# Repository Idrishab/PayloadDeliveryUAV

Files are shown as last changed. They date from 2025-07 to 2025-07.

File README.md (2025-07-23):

# Payload_Delivery_UAV
This project was developed as part of the Aircraft Design course during my undergraduate studies at Kwara State University in 2017. It began as a personal endeavor and later evolved into a course project. The design process focused on manufacturability, with constraints shaped by personal funding and access to local workshops.

The UAV was designed with a maximum takeoff mass (MTOM) constraint of 1.2 kg. Design calculations and optimization were carried out using MATLAB scripts, while CAD modeling was performed in SolidWorks. Aerodynamic properties of various airfoils were analyzed using XFOIL to inform the final design choices.

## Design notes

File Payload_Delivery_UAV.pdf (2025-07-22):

# DESIGN OF A 1.2Kg PAYLOAD DELIVERY UAV

BY

## IDRIS HABEEB BABATUNDE

AS

## ASSESSMENT FOR AIRCRAFT DESIGN

## AAE 401

## DEPARTMENT OF AERONAUTICAL AND ASTRONAUTICAL ENGINEERING

## KWARA STATE UNIVERSITY

## INSTRUCTOR

# DR. YOMI OBIDI

### SUBMISSION DATE: JUNE 15, 2017

## Table of Contents

## ABSTRACT

The design approach used (in this work) is basically the system engineering approach. The detailed description of the design processes and stages involved in this work were presented based on the steps followed.

First pass design was done based on the information acquired from the mission profile, customer design specifications and design objectives. The customer design specifications were incorporated into the conceptual design which provided guidelines through the whole design processes where various adequate equations were applied to obtain the desired parameters. Reasonable guesses were made and various tables were consulted in some instances where there were no available befitting mathematical equations to get the actual required values.

In some instances, the weight of the aircraft is assumed to be constant because it will be using a battery and the payload weight (after dropping it) has no significant change in the weight. Center of gravity (CG) position is also assumed to be constant because the store (for the payload) is situated directly under the CG position which led apparently, to no change in the CG position after releasing the payload.

During the design processes, some parameters of already designed components were reviewed to satisfy the requirements of other components. Federal Aviation Regulations (FAR) were followed and some rules of thumb were applied. Lots of materials resources were also considered to complete this work as all the required information can’t be obtained from a single materials.

# CHAPTER 1

INTRODUCTION
This design is a RC (remote controlled) UAV whose range depends on both battery and transmitter frequency (to maintain transmitter-receiver communication for control) and the endurance depends solely on the battery. The design order is based on the extent of the required parameters which is the reason why the wing was designed immediately after the initial sizing and the tail plane was designed after the wing. The control surfaces were deemed to be designed after all other aircraft components have been designed because of the complexity of the required information.

Aircraft design is an iterative process which requires various parameters to be altered, over and over again, to satisfy various requirements. To make the iteration easy, accurate and to save time, the equations are transformed into MATLAB codes. In calculating the actual lift generated by lifting surfaces, lifting line theory was employed and all the steps involved in it were embedded in a MATLAB program.

Generally, in design, computer aided design (CAD) software are used. The CAD software used for this design is Solidworks. After designing each component, 3D designs of each of the components was produced and were assembled at the end of the whole design process.

# CHAPTER 2

MISSION PROFILE
The aircraft will takeoff within a ground roll of about 8m, climb to an altitude of 15m, within 30 seconds, cruise for some time to cover a distance around 100m, then, loiter around for about 10 seconds to drop a light payload (of about 10g of mass). The aircraft will then return and land with a maximum ground roll of 12m. The flight time will be around 5 minutes and the takeoff mass shouldn’t be more than 1.2kg. The stall speed should not exceed 8m/s and maximum speed should not be less than 15m/s.

From above, the following were deduced:

1. STO = 8m
2. Slanding = 12m
3. Cruise altitude = 15m
4. Vstall = 8m/s
5. Vmax = 15m/s
6. ROC = 15m/30s = 0.5m/s
7. Endurance = 10s
8. Range = about 150m
9. Flight time = 5min
10. MTO = 1.2kg

DESIGN OBJECTIVES
Listed below, are the design objectives commonly considered in designing an aircraft. They were used as guidelines during the design process. Because it is impossible to satisfy all these objectives at once, they were arranged based on their importance to this design.
1. Low cost
2. Control and stability
3. Light weight
4. Ease of manufacture
5. Aerodynamic performance
6. Structural Integrity
7. Heavy payload

# CHAPTER 3

CONCEPTUAL DESIGN
Proposed aircraft: 1.2kg, single engine, prop-driven light-weight UAV

Intended use: object dropping (alternative use is surveillance)

Numbers of seats: no seat

Range: about 150m

Rate of climb: 0.5m/s

Fuel capacity: NIL

Engine selection: Brushless electric motor.

Velocities
1. Max speed: 15m/s
2. Cruise speed: 11.538m/s (i.e. Vmax/1.3)
3. Stall speed: 8m/s
4. Landing speed: 10.4m/s (i.e. 1.3Vstall)

Takeoff and Landing Requirement
1. Takeoff ground roll: 8m
2. Landing ground roll: 12m

Wing Configuration
1. Number of wings: monoplane
2. Wing location: High wing
3. Wing type: Rectangular (because of weight, cost and ease of manufacture)
4. High lift device: Plain flap
5. Shape: Fixed shape
6. Structural configuration: Cantilever

Tail Configuration
1. Tail location: Aft tail
2. Horizontal and vertical tails: conventional tail
3. Attachment: Fixed

Landing Gear Configuration
1. Landing gear mechanism: Fixed

2. Landing gear type: Tricycle
3. Runway: Land based

Manufacturing-Related Item Configuration
1. Material for manufacturing: Foam (Styrofoam, foam board or any other)
2. Assembly technique: use of glue, screws and bolts & nuts

Subsystems Configuration
1. Primary control surfaces: conventional (i.e., elevator, aileron and rudder)
2. Secondary control surface: High lift device (flap)
3. Power transmission: fly-by-wire
4. Fuel tank: inside fuselage (battery)
5. Storage: light object (payload of about 10g)

# CHAPTER 4

FIRST PASS DESIGN
1. Payload mass: 10g
2. Gross weight: 11.772N (i.e. 1.2Kg)
3. Wing loading

Wg
Se

=

ρoVstall

2

2

CLmax
(4.1)
Where ρo = 1.225kg/m³
, Vstall = 8m/s and CLmax was selected to be 1.6

Wg
Se

=

1.225×8

2

2

1.6 = 62.72N/m²
(4.2)

Vlanding = 1.3Vstall = 1.3 × 8 = 10.4m/s
4. Effective wing area,

Se =

Wg
(

Wg
Se

)

=

11.772
62.72

= 0.1878m²
(4.3)
5. Dynamic pressure

q =

ρσVcr

2

2

(4.4)
Where air density and relative density (at cruising altitude (15m)), are 1.2232kg/m³ and 0.9986 respectively. Cruising speed is 11.538m/s

q =

1.2232 ∗ 0.9986 ∗ 11.538²
2

= 81.31N/m²

6. Coefficient of lift at cruise

CL =

Wg⁄Se
q

=

62.72
81.31
= 0.7714 | (4.5)

CL =

1
F

∴ F =

1
CL

=

1
0.7714
= 1.2964 | (4.6)
7. Coefficient of drag

CD = CDP +

CL

2 πeAR | (4.7)

Where CL = 0.7714, CDP was selected to be 0.025, e to be 0.825 and AR to be 7

CD = 0.025 +

0.7714
π × 0.825 × 7

= 0.0578
8. L
D

=

CL
CD

=

0.7714
0.0578
= 13.346 | (4.8)
9. D = Wg ∙

CD
CL

= 11.772 ×

1
13.346
= 0.8821N | (4.9)
10. Thrust horsepower required at cruise altitude THP =

DVcr
745.7

=

0.8821∗11.538
745.7
= 0.01365ℎp (10.177W) | (4.10)
11. Maximum brake horsepower (BHP)

BHPcr =

THP

ηprop

⁄0.7 | (4.11)

ηprop was selected to be 0.85 BHPcr =

0.01365
0.85
⁄0.7 = 0.0229ℎp (17.1W) | (4.12)

BHP at sea level = BHPcr (

ρo
ρ

)

0.96
= 0.0229 (

1.225
1.2232)

0.96
= 0.023ℎp (4.13)
12. Optimum cruise lift coefficient
CL = √π ∙ e ∙ AR ∙ CDP = √π ∙ 0.825 ∙ 7 ∙ 0.025 | (4.14)

= 0.6735
Optimum Vcr = √
Wg
ρ
2

σ∙CLcropt

∙Se∙F

= √
11.772
1.2232
2

×0.6735×0.1878×1.2964

= 10.834m/s (4.15)

13. Power required to satisfy the required ROC:
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
3CDo
K

(

W
S

)∙(
1.155
(L⁄D)ηp

)

| (4.16)

Where W/P is the power loading, ROC is the rate of climb, ηp is the propeller efficiency, ρ is the air density at sea level, CDo is the zero lift drag coefficient, K is the induced drag factor, (W/S) is the wing loading, and (L/D) is the lift to drag ratio.
K =
1 π∙e∙AR | (4.17)

K =

1
3.142 × 0.825 × 7

= 0.0551

ROC has been stated earlier to 0.5m/s and CDo was selected to be 0.035.
(

W
P

) =

1

0.5
0.85 +

√
2
1.225 × √
3 × 0.035
0.0551

× 62.72 × (

1.155
13.346 × 0.85)

= 0.6636N/W

P =

W
(

W
P

)

(4.18)

P =

11.772
0.6636 = 17.7W

Therefore, the power required is 17.7W

FIRST PASS FINAL RESULT

1. Gross weight, Wg = 11.772N
2. Wing loading = 62.7N/m²
3. Stall velocity = 8m/s
4. Wing area = 0.1878m²

5. Dynamic pressure, q = 81.3N/m²
6. Total drag coefficient, CD = 0.0578
7. Lift to drag ratio = 13.346
8. Drag, D = 0.8821N
9. Thrust horsepower (THP) = 0.0136hp (10.177W)
10. Brake horsepower at cruise altitude (BHP)cr = 0.0229 (17.1W)
11. BHP at sea level = 0.023hp
12. Optimum cruise lift coefficient = 0.6735
13. Optimum cruise speed = 10.834m/s
14. ROC = 0.5m/s

SECOND PASS DESIGN
Second pass design wasn’t considered (because it involves obtaining a more accurate gross weight); the gross weight used during first pass design was stated as a requirement. Fuel and oil weights aren’t needed because the aircraft will be using a RC electric motor and battery. Second pass design also optimizes the wing area, drag and brake horsepower at sea level by multiplying them by a conversion factor (calculated using a new gross weight). Since the gross weight won’t be altered, these and other parameters obtained from first pass design will remain the same.

# CHAPTER 5

WING AIRFOIL SELECTION
PRACTICAL STEPS IN SELECTING AN AIRFOIL
1. Aircraft weight: 11.772N
2. Aircraft ideal cruise lift coefficient (CLC): CLC =

2Wavg
ρVC

2S

(5.1)

CLC =

2 × 11.772
1.2232 × 10.834² × 0.1878 = 0.8732
3. Wing cruise lift coefficient (CLCW ).

CLCW

=

CLC
0.95

(5.2)

CLCW

=

0.8732
0.95 = 0.9191
4. Wing airfoil ideal lift coefficient (Cli):

Cli =

CLCW

0.9

(5.3)

Cli =

0.9191
0.95 = 1.0212
5. Aircraft maximum lift coefficient (CLmax):

CLmax =

2WTO
ρ0Vs

2S

(5.4)

Where Vs is the aircraft stall speed, ρo is the air density at sea level, and WTO is the aircraft maximum take-off weight.

CLmax =

2 × 11.772
1.225 × 8

2 × 0.1878 = 1.6

6. Wing maximum lift coefficient (CLmax _w ).

CLmax _w =

CLmax
0.95

(5.5)

CLmax _w =

1.6
0.95 = 1.6832
7. Airfoil gross maximum lift coefficient (Clmax_gross):

Clmax _gross =

CLmax _w
0.9

(5.6)

Clmax _gross =

1.6832
0.9

= 1.8703

8. High lift device (HLD): Plain Flap.
9. HLD contribution to the wing maximum lift coefficient (ΔClHLD): 0.55.

10. Wing airfoil net maximum lift coefficient (Clmax):
Clmax = Clmax _gross − ∆ClHLD = 1.3203 | (5.7)
11. Reynolds number: 100,000 (using cruise speed and chord length of 10.834m/s and 0.16m respectively)

The following airfoils were considered

1. SD7037
2. E193
3. S9000
4. Clark Y

At Reynolds number of 100000, the values for various parameters (as shown in the table below) were obtained for the airfoils. These values were obtained with the aid of system software (XFOIL) and a website (www.airfoiltools.com)

AIRFOIL
PARAMETERS

AIRFOILS
| SD7037 | E193 | S9000 | CLARK Y
Clmax | 1.3364 | 1.283 | 1.2702 | 1.3663
Alfas (deg) | 12 | 12 | 11 | 12
Alfa0 (deg) | -1.7679 | -3.2868 | -1.2702 | -2.2492
Cl0 | 0.3046 | 0.4068 | 0.2071 | 0.3713
Cdmin | 0.01519 | 0.01452 | 0.01311 | 0.01722
Cli | 0.04 | 0.24 | 0.08 | 0.8
(Cl/Cd)max | 55.2 | 58.7 | 53.3 | 53
Clalfa | 6.0628 | 6.1183 | 6.0628 | 6.1852
Cmmin | -0.084 | -0.096 | -0.073 | -0.092
S.Q. | Moderate | Abrupt | Moderate | Docile
Max. thickness (unit) | 0.092 | 0.102 | 0.09 | 0.1171

From these, Clark Y airfoil was selected.

Table 5.1: Airfoil data

WING DESIGN
STEP 1: Wing incidence

The selected airfoil ideal lift coefficient is 0.8. Since at ideal lift coefficient, minimum drag is experienced, the angle of attack corresponding to the ideal lift coefficient was set as the wing incidence (or wing setting angle). To obtain this value, a reference was made to the Cl-α curve (through the use of XFOIL).

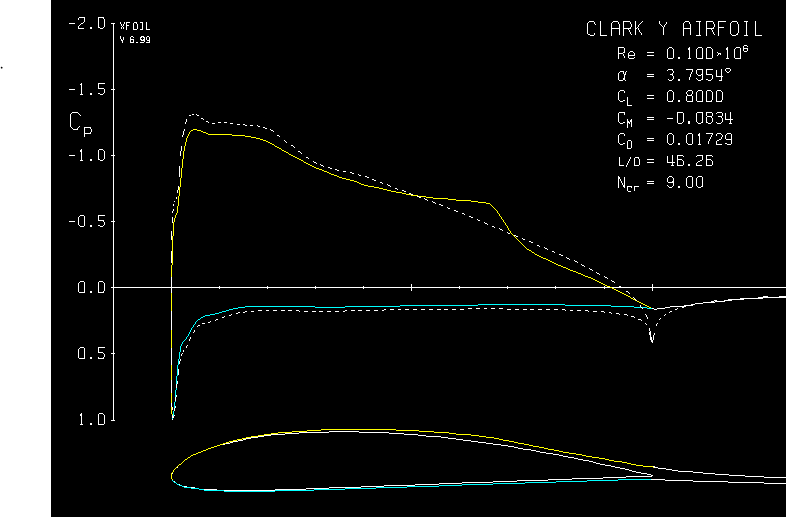
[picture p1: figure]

Therefore, wing setting angle (αset) or wing incidence (iw) is equal to 3.7954 deg.

STEP 2: ASPECT RATIO

Considering the various advantages and disadvantages of high and low values, aspect ratio was selected to be 7.

STEP 3: TAPER RATIO

The effects of taper ratio was carefully considered but for some reasons (such as ease of manufacturing, cost and to keep the design simple) the wing was left straight i.e. no taper.

Fig 5.1: wing setting angle from XFOIL

STEP 4: SWEEP ANGLE:

It was stated (in ref 1) that If the aircraft maximum speed is less than Mach 0.3 (the borderline to include the compressibility effect), no sweep angle is recommended for the wing, since its disadvantages will negate all the improvement produced. For this reason and some others, no sweep angle was considered.

STEP 5: TWIST ANGLE

This design will use no twist angle. Though, twist angle have the advantages of avoiding tip stall before root stall and modification of the lift distribution to an elliptical one but it give rise to reduction in lift. In addition, the complexity of manufacturing, increase in weight as well cost required prevent its use.

STEP 6: DIHEDRAL ANGLE

No dihedral.

STEP 7: REQUIRED LIFT COEFFICIENT DURING CRUISE:

CLC =

2Wavg
ρVc

2S

(5.8)

CLC =

2 × 11.7720
1.2232 × 10.834² × 0.1878 = 0.8732
STEP 8: REQUIRED AIRCRAFT TAKEOFF LIFT COEFFICIENT:
VTO = kVstall | (5.9)

Where k is 1.1 for fighter aircraft and 1.2 for general aviation (GA) aircraft

VTO = 1.2 × 8 = 9.6m/s

CLTO =

2WTO
ρVTO

2 S

(5.10)

CLTO =

2 × 11.7720
1.225 × 9.6

2 × 0.1878 = 1.1105

STEP 9: WING INCIDENCE FROM LIFTING LINE THEORY TO SATISFY CRUISE CL

A MATLAB code has been written (in Ref 1) for lifting line theory which divides the wing into sections to calculate the lifts generated per section. They were then summed up to obtain the total lift produced by the wing at that incidence. This MATLAB program has lift distribution curve incorporated in it.

The following were used in calculating lift coefficient at cruise

1. Wing area = 0.1878m²
2. Aspect ratio = 7
3. Taper ratio = 1
4. Twist angle = 0
5. Wing setting angle = 3.7954deg
6. Airfoil lift curve slope = 6.1852rad⁻¹
7. Zero-lift angle of attack = -2.2492deg

MATLAB CODE

clc
clear
N = 9; % (number of segments - 1) S = 0.1878; % m^2
AR = 7; % Aspect ratio
lambda = 1; % Taper ratio
alpha_twist = -1e-8; % Twist angle (deg)
i_w = 3.7954; % wing setting angle (deg)
a_2d = 6.1852; % Airfoil lift curve slope (1/rad) alpha_0 = -2.2492; % zero-lift angle of attack (deg)
b = sqrt(AR*S) % wing span (m)
MAC = S/b % Mean Aerodynamic Chord (m)
Croot = (1.5*(1+lambda)*MAC)/(1+lambda+lambda^2); % root chord (m) theta = pi/(2*N):pi/(2*N):pi/2;
alpha = i_w+alpha_twist:-alpha_twist/(N-1):i_w;
% segment’s angle of attack
z = (b/2)*cos(theta);
c = Croot * (1 - (1-lambda)*cos(theta)); % Mean Aerodynamics Chord at each segment (m)
mu = c * a_2d / (4 * b);
LHS = mu .* (alpha-alpha_0)/57.3; % Left Hand Side
% Solving N equations to find coefficients A(i):
for i=1:N
for j=1:N
B(i,j) = sin((2*j-1) * theta(i)) * (1 + (mu(i) * (2*j-1)) /sin(theta(i))); end
end
A=B\transpose(LHS);
for i = 1:N
sum1(i) = 0;
sum2(i) = 0;
for j=1:N
sum1(i) = sum1(i) + (2*j-1) * A(j)*sin((2*j-1)*theta(i)); sum2(i) = sum2(i) + A(j)*sin((2*j-1)*theta(i));
end
end
CL = 4*b*sum2 ./ c;
CL1=[0 CL(1) CL(2) CL(3) CL(4) CL(5) CL(6) CL(7) CL(8) CL(9)]; y_s=[b/2 z(1) z(2) z(3) z(4) z(5) z(6) z(7) z(8) z(9)]; plot(y_s,CL1,'-o')
grid title('Lift distribution') xlabel('Semi-span location (m)') ylabel ('Lift coefficient') CL_wing = pi * AR * A(1)

With these, the lift coefficient produced by the wing is 0.4898. The wing incidence was then varied via trial and error to obtain the required lift coefficient at cruise. At a wing incidence of 8.53deg, the generated wing lift coefficient is 0.8735. Although, this satisfies cruise requirement (based of lift coefficient) but the incidence is too high and the design has to be reviewed.

The major aim of reviewing the design is to reduce the required cruise lift coefficient which can easily be done by increasing the cruise speed. Cruise speed is a function of maximum speed (Vcr = Vmax/1.3). Therefore, maximum speed was adjusted to 19m/s. first pass design was then reviewed and the following are the new data:

1. Gross weight, Wg = 11.772N
2. Wing loading = 62.7N/m²
3. Stall velocity = 8m/s
4. Cruise speed = 14.6154m/s
5. Maximum speed = 19m/s
6. Landing speed = 10.4m/s
7. Wing area = 0.1878m²
8. Dynamic pressure, q = 130.4605N/m²
9. Cruise lift coefficient = 0.4808
10. Total drag coefficient, CD = 0.0377
11. Lift to drag ratio = 12.7394
12. Drag, D = 0.9241N
13. Thrust horsepower (THP) = 0.0181hp (13.497W)
14. Brake horsepower at cruise altitude (BHP)cr = 0.0304 (22.67W)
15. BHP at sea level = 0.0305hp (22.74W)
16. ROC = 0.5m/s

While reviewing airfoil selection criteria, the new required airfoil ideal lift coefficient is 0.5612. Reynolds number also changes to 150,000. At this Reynolds number, Clark Y airfoil has the following parameters:

1. Zero-lift angle of attack = -3.1264deg
2. Lift at zero AOA = 0.4345
3. Maximum Cl = 1.3769

4. Stall AOA = 13deg
5. Cdmin = 0.01244
6. Cli = 0.49
7. (L/D)max = 64.68
8. Cmmin = -0.099
9. Clα = 6.1852rad⁻¹

While reviewing wing design the following steps has these new results:

Step1: wing incidence equals 0.5327deg

Step 7: required lift coefficient during cruise is 0.48

With the use of the same MATLAB program, at a wing incidence of 2.8deg, the lift generated is 0.4808 and the lift distribution is as in the figure below. Therefore, the wing incidence was set to be 2.8deg.

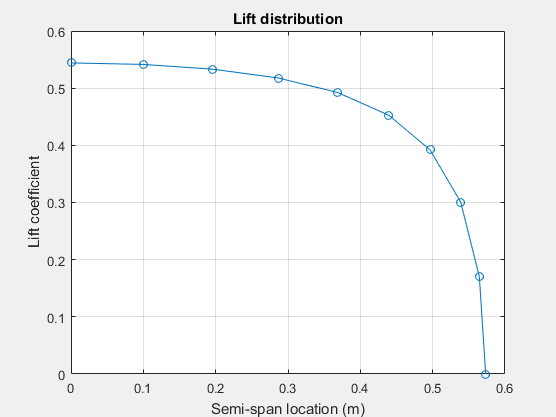
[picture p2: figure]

Although, the lift distribution is not elliptical but can be worked with as it is close to elliptical lift distribution. To achieve an elliptical lift distribution, the twist angle will have to be altered (to

Fig 5.2: Lift distribution around -1.5deg). Considering ease of manufacturing, light weight and cost; the twist angle was left unaltered.

STEP 10: FLAP DESIGN

In designing the flap, flap; span to wing span ratio (bf/b); chord to wing chord ratio (Cf/C) and; maximum deflection (δfmax) were used. The latter two were used to determine the approximate increment in the wing zero-lift angle of attack (due to flap deflection) through the use of the following equation:

∆∝o≈ −1.5 ∙

Cf
C
δf | (5.11)

Flap span to wing span ratio was used to determine the flap region across the span. These were incorporated into the MATLAB code for lifting line theory to determine the total lift generated by the wing (with flap down).

As an initial value, the following were used: Cf/C = 20%, bf/b = 60% and δf = 13deg and αTO = 9deg (wing angle of attack at takeoff)

With these, the total lift generated is 1.1863. When the wing angle of attack was set to 8.07deg, the lift generated by the wing is 1.1109. The wing angle of attack was reduced because of stall; the wing stalls earlier when flap is deflected.

MATLAB CODE WITH FLAP DEFLECTED

clc
clear
N = 9; % (number of segments-1) S = 0.1878; % m^2
AR = 7; % Aspect ratio
lambda = 1; % Taper ratio
alpha_twist = -1e-10; % Twist angle (deg)
i_w = 8.07; % wing setting angle (deg)
a_2d = 6.1852; % lift curve slope (1/rad)
a_0 = -3.1264; % flap up zero-lift angle of attack (deg)
cf_c=0.2; %flap to wing chord ratio
df=13; %flap deflection(deg)
a_0_fd = 2*(-1.15*cf_c*df); % flap down zero-lift angle of attack (deg) b = sqrt(AR*S); % wing span
bf_b=0.6; %flap-to-wing span ratio
MAC = S/b; % Mean Aerodynamic Chord
Croot = (1.5*(1+lambda)*MAC)/(1+lambda+lambda^2); % root chord theta = pi/(2*N):pi/(2*N):pi/2; alpha=i_w+alpha_twist:-alpha_twist/(N-1):i_w;
% segment’s angle of attack
for i=1:N

if (i/N)>(1-bf_b)
alpha_0(i)=a_0_fd; %flap down zero lift AOA else
alpha_0(i)=a_0; %flap up zero lift AOA
end
end
z = (b/2)*cos(theta);
c = Croot * (1 - (1-lambda)*cos(theta)); % MAC at each segment mu = c * a_2d / (4 * b);
LHS = mu .* (alpha-alpha_0)/57.3; % Left Hand Side
% Solving N equations to find coefficients A(i):
for i=1:N
for j=1:N
B(i,j) = sin((2*j-1) * theta(i)) * (1 + (mu(i) * (2*j-1)) / sin(theta(i))); end
end
A=B\transpose(LHS);
for i = 1:N
sum1(i) = 0;
sum2(i) = 0;
for j=1:N
sum1(i) = sum1(i) + (2*j-1) * A(j)*sin((2*j-1)*theta(i)); sum2(i) = sum2(i) + A(j)*sin((2*j-1)*theta(i));
end
end
CL_TO = pi * AR * A(1)

SUMMARY OF WING PARAMETER

1. Number of wings: monoplane
2. Wing vertical location: High wing
3. Airfoil section: Clark Y
4. Wing setting angle or wing incidence, iw = 2.8 deg
5. Takeoff wing angle of attack, ∝TOw
= 8.07deg (i.e. the fuselage will pitch up by 8.07 – 2.8 = 5.27deg)
6. AR = 7
7. Wing span, b = √(AR* S) = √(7*0.1878) = 1.1466m
8. Wing chord, C = S/b = 0.1878/1.1466 =0.164m (16.4cm)
9. Taper ratio = 1 i.e. root chord = tip chord = 0.164m
10. Sweep angle = 0 deg
11. No twist
12. Dihedral angle = 0 deg
13. Flap chord, Cf = 0.2 * C =0.2 * 0.164 =0.0328m (3.28cm)
14. Flap span, bf = 0.6 * b = 0.6 * 1.1466 = 0.6885m (68.8cm)
15. Flap deflection at takeoff = 13deg

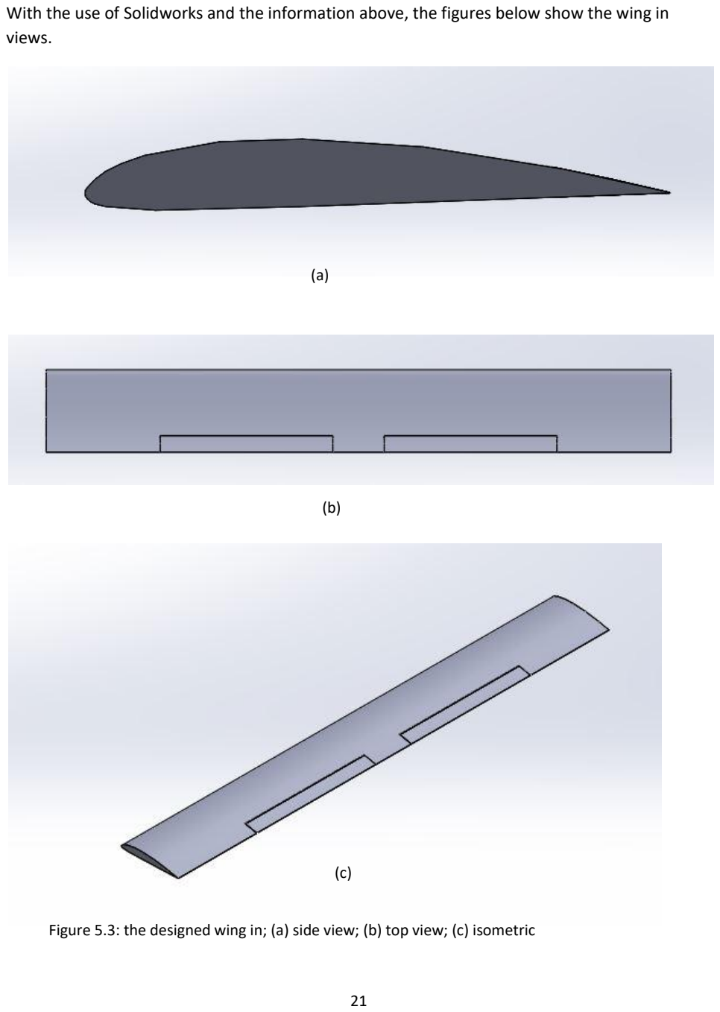
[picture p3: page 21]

With the use of Solidworks and the information above, the figures below show the wing in views.

(a)

Figure 5.3: the designed wing in; (a) side view; (b) top view; (c) isometric

(c)

(b)

# CHAPTER 6

TAIL DESIGN
PRACTICAL DESIGN STEPS
STEP 1: Tail Configuration Selection – Conventional Tail

HORIZONTAL TAIL DESIGN

STEP 2: Horizontal Tail Location (Aft or Forward (Canard)) – Aft
STEP 3: Horizontal Tail Volume Coefficient (VH) Selection

Considering the effect of high and lower value of this parameter, VH was selected to be 0.6 as an initial value

STEP 4: Calculation Of Optimum Tail Moment Arm (lopt) To Minimize the Aircraft Drag and Weight

Optimum arm was calculated using the equation below:

lopt = Kc√
4CSVH
πDf

(6.1)

Where, Kc is the correction factor which compensates for fuselage aft section deviation from conical shape (it is between 1 and 1.4), C is the wing MAC, S is the wing area, VH is the horizontal tail volume coefficient and Df is the maximum fuselage diameter. Kc was selected to be 1.1 and Df was set to be 10cm.

∴ lopt = 1.1 × √
4 × 0.164 × 0.1878 × 0.6
π × 0.1

= 0.5335m = 53.35cm

From table 2 below, tail arm to total aircraft length ratio was selected to be 0.6. Therefore, total aircraft length is 0.8892m.

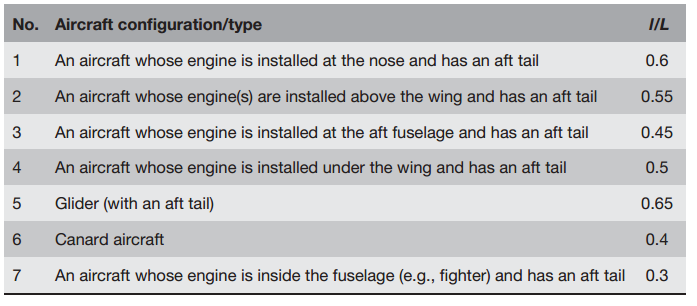
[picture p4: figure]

STEP 5: Horizontal Tail Planform Area, Sh

Sℎ =

VHSC
lℎ

(6.2)

∴ Sℎ =

0.6 × 0.164 × 0.1878
0.5335 | = 0.0346m²
STEP 6: Wing/Fuselage Aerodynamic Pitching Moment Coefficient (Cmo_wf) Calculation

This can be calculated using the following equation:

Cm0_wf = Cmaf ∙

ARcos²
(Λ)
AR+2cos (Λ)

+ 0.01αt
(6.3)

Where Cmaf is the wing airfoil section pitching moment coefficient, AR is the wing aspect ratio, Λ is the wing sweep angle, and αt is the wing twist angle (in degrees).

The airfoil for this design is CLARK Y and its pitching moment is -0.099. From wing design, AR is 7, sweep angle and twist angle are zero

Cm0_wf = −0.099 ∙

7 × cos²
(0)
7 + 2cos (0)

+ 0.01(0) = −0.077

STEP 7: Cruise Lift Coefficient, CLC

It has been calculated earlier to be 0.48.

Table 6.1: Typical values of l/L for various aircraft configurations

STEP 8: Calculation of Horizontal Tail Desired Lift Coefficient at Cruise from Trim Equation

The trim equation was derived (in Ref 1) to be:

Cmo_wf + CLC

(ℎ − ℎo

) − ηℎVHCLℎ = 0 | (6.4)
Where Cmo_wf is the wing/fuselage aerodynamic pitching moment, CLC | is the aircraft cruise lift
coefficient, ηh is the horizontal tail efficiency (which is not always 100% because of wake and downwash and was selected to be 90% or 0.9), VH is the horizontal tail volume coefficient and CLC is the aircraft cruise lift coefficient.

The variable ho denotes the non-dimensional wing/fuselage aerodynamic center (

Xacwf

C

)

position. A typical value for ho is about 0.2–0.25 for the majority of aircraft configurations. The parameter h denotes the non-dimensional aircraft cg position(

Xcg
C
| ). The typical values for the

aircraft non-dimensional center of gravity limit are: h =0.1 to 0 .3. Therefore, the values for h and ho are selected to be 0.2 and 0.25 respectively.

Equation (14) was rearranged as:

CLℎ =

Cmo_wf+CLC

(ℎ−ℎo) ηℎVH | (6.5)

CLℎ =

−0.077 + 0.48(0.2 − 0.25)
0.9 × 0.6

= −0.1870

Therefore, the desired horizontal tail lift coefficient is -0.1870

STEP 9: Horizontal Tail Airfoil Section Selection

The following are considered in selecting the horizontal tail airfoil:

1. Symmetric airfoil
2. Minimum drag
3. Large lift curve slope
4. Lower maximum thickness compared to the wing airfoil

The horizontal tail airfoil section was selected to be NACA 0008 which has the following properties at Reynolds number of 150,000:

1. Zero-lift angle of attack (αo) is zero
2. Stall angle of attack is 8deg
3. Lift curve slope is 6.0176 1/rad
4. Ideal lift coefficient (Cli) is 0
5. Maximum Thickness to chord ((t/C)max) is 8%
6. Clmax is 0.77
7. Cdmin is 0.00958
8. Minimum Pitching moment is -0.009
9. Maximum (L/D) is 38.77

Lift curve slope (1/rad) was calculated using the following equation:

Clα =

dCl
dα

= 1.8π (1 + 0.8(

t⁄c)max) | (6.6)
STEP 10: Selection of Horizontal Tail Sweep Angle and Dihedral

As an initial value, the sweep and dihedral angles were set to be zero degree.

STEP 11: Horizontal Tail Aspect Ratio and Taper Ratio

Considering the effects of aspect ratio on the horizontal tail, the initial value for aspect ratio was calculated using this relationship

ARℎ =

2
3
ARw | (6.7)

ARℎ =

2
3

× 7 = 4.667

The horizontal tail taper ratio was selected to be 0.7

STEP 12: Calculation of Horizontal Tail Lift Curve Slope, CLα_h

The horizontal tail lift curve slope was determined with the following equation:

CL∝_ℎ =

dCLℎ
dαℎ

=

Cl∝_ℎ 1+ Cl∝_ℎ π∙ARℎ | (6.8)

Where Cl∝_ℎ
is the horizontal tail airfoil lift curve slope.

CL∝_ℎ =

6.0176

1 +

6.0176
π ∙ 4.667

= 4.2666 rad⁻¹

STEP 13: Horizontal Tail Angle Of Attack at Cruise

αℎ =

CLℎ

CL∝_ℎ

(6.9)

αℎ =

−0.187
4.2666 = −0.04383rad (−2.511deg)
STEP 14: Downwash Angle (ε) at the Tail

The downwash is a function of wing angle of attack (αw) and is determined as follows:

ε = εo +

∂ε
∂α αw | (6.10)
Where εo (downwash angle at zero angle of attack (in rad)) and ∂ε | ∂α (downwash slope) are found

as:

εo =

2CLw
π∙AR
| (6.11)

∂ε
∂α =
2CL∝_w π∙AR | (6.12)

Where ∝w is the wing setting angle (in rad), CLw

is the wing lift coefficient at cruise, CL∝_w | is the
wing lift curve slope (rad⁻¹
) and AR is the wing aspect ratio.

From wing design, the following were obtained:

1. CL∝_w = 4.8276 rad⁻¹
2. AR = 7
3. CLw = CLC = 0.48 (since horizontal tail is to be design to satisfy cruise conditions)
4. ∝w= 2.8 deg (0.04887rad)

∂ε
∂α =

2 × 4.8276
π × 7

= 0.4390 rad/rad

εo =

2 × 0.48
π × 7

= 0.0436 rad

ε = 0.0436 + 0.4390 ∙ 0.04887 = 0.0651 rad

STEP 15: Horizontal Tail Incidence Angle, ih

Due to the presence of the downwash at the horizontal tail location, the tail effective angle of attack is defined as:

∝ℎ= ∝f+ iℎ − ε | (6.13)

Where ∝f is the fuselage angle of attack at cruise (which is zero), αℎ is the horizontal tail angle of attack (Calculated at step 13).

iℎ =∝ℎ −∝f+ ε | (6.14)

iℎ = (−0.04383) − 0 + 0.0651 = 0.02127rad (1.2187deg)

STEP 16: Tail Span, Tail Root Chord, Tail Tip Chord, and Tail MAC

The following equations were used to obtain the values of horizontal tail span; root chord; tip chord; and MAC (or C)

ARℎ =

bℎ Cℎ | (6.15)

ARℎ =

bℎ

2 Sℎ | (6.16)

λℎ =

Cℎtip Cℎroot | (6.17)

Cℎ =

2
3

Cℎroot (

1+λℎ+λℎ

2

1+λℎ

) | (6.18)

On rearranging the equations above, I have the following:

bℎ = √ARℎ × Sℎ | (6.19)

Cℎ =

bℎ ARℎ | (6.20)

Cℎroot =

Cℎ
2/3(
1+λℎ+λℎ

2

1+λℎ

)

(6.21)

Cℎtip = λℎ × Cℎroot | (6.22)

Therefore;

bℎ = √4.667 × 0.0346 = 0.402m

Cℎ =

0.402
4.667 = 0.0862m

Cℎroot =

0.0862
2/3(

1 + 0.7 + 0.7

2
1 + 0.7

)

= 0.1004m

Cℎtip = 0.7 × 0.1004 = 0.07028m

STEP 17: Calculation of Horizontal Tail Lift Coefficient at Cruise (Using Lifting Line Theory)

To do this, the tail was treated as a small wing and the following parameters were used:

1. Horizontal tail area (0.0346m²
)
2. Horizontal tail aspect ratio (4.667)
3. Horizontal tail taper ratio (0.7)
4. Tail angle of attack (-2.511 deg)
5. Tail airfoil lift curve slope (6.0176 rad⁻¹ )
6. Airfoil zero lift angle of attack (0 deg)
7. Tail span (0.402m)
8. MAC (0.0862m)
9. Root chord (0.1004m)

To calculate the lift generated by the horizontal tail, the same MATLAB code that was used to for the wing lift was used. With the parameters above, the lift generated by the tail is -0.1818

MATLAB CODE

clc
clear
N = 9; % (number of segments-1) Sh = 0.0346; % m ˆ 2
ARh = 4.667; % Aspect ratio
lambdah = 0.7; % Taper ratio
alpha_twist = 1e-8; % Twist angle (deg)
a_h = -2.511; % tail angle of attack (deg)
a_2d = 6.0176; % tail airfoil lift curve slope (1/rad) alpha_0 = 0; % Airfoil zero-lift angle of attack (deg)
b = sqrt(ARh*Sh); % tail span
Chroot = 0.1004; % root chord
MAC = (2/3)*Chroot*(1+lambdah+lambdah^2)/(1+lambdah); % Mean Aerodynamic Chord
theta = pi/(2*N):pi/(2*N):pi/2; alpha=a_h+alpha_twist:-alpha_twist/(N-1):a_h;% segment’s angle of attack
z = (b/2)*cos(theta);
c = Chroot * (1 - (1-lambdah)*cos(theta)); % Mean Aerodynamics chord at each segment
mu = c * a_2d / (4 * b);
LHS = mu .* (alpha-alpha_0)/57.3; % Left Hand Side

% Solving N equations to find coefficients A(i):
for i=1:N
for j=1:N
B(i,j)=sin((2*j-1) * theta(i)) * (1+(mu(i) *(2*j-1))/sin(theta(i))); end
end
A=B\transpose(LHS);
for i = 1:N
sum1(i) = 0;
sum2(i) = 0;
for j=1:N
sum1(i) = sum1(i) + (2*j-1) * A(j)*sin((2*j-1)*theta(i)); sum2(i) = sum2(i) + A(j)*sin((2*j-1)*theta(i));
end
end
CL_htail = pi * ARh * A(1)
STEP 18: Adjustment of the Horizontal Tail Angle Of Attack to Meet the Required Lift Coefficient

The lift coefficient required from the horizontal tail is -0.1870. The result obtained at step 17 is not the required lift coefficient. Therefore, the angle of attack was adjusted through trial and error with the same MATLAB program. On doing this, the horizontal tail was found to have this lift coefficient at -2.59 deg.

The horizontal tail incidence was recalculated as:

iℎ = (−2.59deg) − 0 + (0.0651rad ×

57.3deg
1rad ) = 1.14deg
STEP 19: Checking Of Horizontal Tail Stall

The tail airfoil was expected to stall at 8ᵒ, the tail setting angle is 1.14ᵒ, meaning that the fuselage will pitch up to 6.86ᵒ before the tail stalls. The wing setting angle is 2.8deg and the airfoil will stall at 13deg. Therefore, the fuselage will pitch up to 10.2deg meaning that horizontal tail will stall before the wing which must be prevented.

STEP 20: Design Review

To avoid this, another airfoil (Naca0010) which stalls later than the current airfoil was selected. The airfoil has the following parameters (at Re = 150,000):

1. Clmax = 0.91
2. Stall angle = 10ᵒ
3. Zero-lift angle of attack = 0
4. Lift curve slope = 6.108rad⁻¹

5. Cdmin = 0.01037
6. Cmmin = -0.02
7. (t/c)max = 10% or 0.1
8. (L/D)max = 41.09

Based on these, the following are the new values:

1. Horizontal tail lift curve slope = 4.3118rad⁻¹
2. Initial tail angle of attack = -0.04337rad (-2.485deg)
3. Tail angle of attack = 2.56deg
4. Tail incidence = 1.17deg

On checking stall, the tail stalls when fuselage pitches up to 8.83deg. Since the tail still stall earlier than the wing, some parameters that will reduce the tail incidence were looked into.

To reduce the tail angle of attack, the negative value of the desired tail lift coefficient has to be reduced which is a function of tail volume coefficient. Reducing the tail volume coefficient will increase the desired tail lift coefficient’s negative value.

After considering effects of some values of tail volume coefficient, it was set to be 0.3. With this the following are the new revised values:

1. Horizontal tail volume coefficient, VH = 0.3
2. Optimum arm, lopt = 0.3773m
3. Aircraft length, L = 0.6288m
4. Horizontal tail area, Sh =0.0245m²
5. Desired horizontal tail lift coefficient, CLh = -0.374
6. Horizontal tail span, bh = 0.3381m
7. Horizontal tail MAC, Ch = 0.0724m
8. Horizontal tail root chord, Ch_root = 0.0844m
9. Horizontal tail tip chord, Ch_tip = 0.059m
10. Horizontal tail setting angle from lifting line theory, αh = -5.12deg
11. Horizontal tail incidence (with downwash effect), ih = -1.39deg
12. The tail airfoil stalls when fuselage pitches up to 11.39deg and wing stalls when fuselage pitches up to 10.2deg.
STEP 21: STATIC MARGIN CHECK

Static margin which is a measure of the degree of stability or instability of an aircraft was calculated using:

SM =

xnp−xcg
c

(6.23)

Where, xnp is the neutral point position on the wing.

xnp
C

≃

1
4

+

1+2⁄AR
1+2⁄ARℎ

(1 −
4
AR+2
) VH | (6.24)

xnp
C

≃

1
4

+

1 + 2⁄7
1 + 2⁄4.667 ∙ (1 −

4
7 + 2

) ∙ 0.3 ≃ 0.4

Equation (33) can be rewritten as:

SM =

xnp
C

−

xcg
C

(6.25)

It was recalled that the distance between wing leading edge and aircraft center of gravity (CG) is hC (i.e. h multiplied by MAC). Mathematically;

xcg = ℎC | (6.26)

Therefore,

ℎ =

xcg C | (6.27)

h was earlier stated as 0.2. Then, static margin is:

SM = 0.4 − 0.2 = 0.2

This means that the aircraft is reasonably stable. In Ref 3, it was stated that “a well behaved aircraft typically has a VH value which falls in the range of 0.3 and 0.6”. And in Ref 1, it was stated that “the typical value for static margin is from 0.1 to 0.3”

The position of the aircraft CG location on the wing was calculated as:

xcg = ℎ × C = 0.2 × 0.164 = 0.0328m | (6.28)

Meaning that, the CG is 3.28cm from the wing leading edge.

STEP 22: Calculation of Horizontal Tail Contribution to the Static Longitudinal Stability Derivative (Cmα).

For the aircraft to be stable, Cmα must be negative. Cmα can be expressed as:

Cmα = CLα_wf(ℎ − ℎo

) − CLα_h
ηh

Sh
S

(

l
C

− h) (1 −

dε
dα
) | (6.29)

All these parameters have been described and obtained earlier; their values were just slotted into the equation. CLα_wf is the wing/fuselage lift curve slope and was set to be the same as wing lift curve slope. All the angles were considered in radians. ηh is the horizontal tail efficiency.

Cmα = 4.8276(0.2 − 0.25) − 4.2666 ∙ 0.9 ∙

0.0245
0.1878 ∙ (

0.3773
0.164 − 0.2) (1 − 0.4390)

= −0.83rad⁻¹
The table below was used as a guideline.
STEP 23: Analysis of the Dynamic Longitudinal Stability

The dynamic longitudinal stability analysis is performed after all aircraft components are designed and the roots (λ) of the longitudinal characteristic equation are calculated. A general form of the aircraft longitudinal characteristic equation looks like the following:

A1λ

4 + B1λ

3 + C1λ

2 + D1λ + E1 = 0 | (6.30)

The longitudinal stability derivatives cannot be determined unless all aircraft components, including wing and fuselage, have been designed. This is why it was resorted to a simplifying criterion that could be a base for the horizontal tail preliminary design; when the horizontal tail volume coefficient (VH) is close to the ballpark number as stated in step 21, it is 90% confident that the longitudinal stability requirements have been satisfied.

Table 6.2: The static and dynamic longitudinal and directional stability requirements

STEP 24: Horizontal Tail Vertical Location

To avoid deep stall, the following experimental equations were recommended for the initial approximation of the horizontal tail vertical height [1]:

ℎt > l ∙ tan(αs − iw + 3) | (6.31)
ℎt < l ∙ tan(αs − iw − 3) | (6.32)

Where αs is the wing stall angle (in degrees) and iw is the wing setting angle (in degrees). The first equation is for horizontal tail above the wing level while the second is for tail below wing level. The second equation was used because the design is high wing and the horizontal tail is to be mounted on the fuselage.

ℎt < 0.3773 ∙ tan(13 − 2.8 − 3)

ℎt < 0.0477m

A MATLAB code was written for all of the processes involved in horizontal tail design which made the iterations easier.

MATLAB CODE

clc
clear
VH = 0.3; % horizontal tail volume coefficient Kc = 1.1; % Fuselage aft shape correction factor MAC = 0.164; % wing MAC (m)
S = 0.1878; % Wing area (m^2)
Df = 0.1; % Fuselage diameter (m)
lL = 0.6; % Ratio of horizontal tail arm to aircraft legnth Cm_af = -0.099; % wing airfoil pitching moment
AR = 7; % Wing aspect ratio
swp = 0; % Wing sweep angle (deg)
alfa_twist = 0; % Wing twist angle (deg)
Wavg = 11.772; % Aircraft average weight (N)
Vc = 14.6154; hc = 15; % Cruise speed (m/s) and cruise altitude (m) nh = 0.9; % Horizontal tail (HT) efficiency
h = 0.2; % Center of gravity limit (m/m)
ho = 0.25;% Wing/fuselage aerodynamic center (m/m)
swp_h = 0; % HT sweep angle (deg)
dihed = 0; % HT dihedral angle (deg)
lambdah = 0.7;% HT taper ratio
ARh = 2*AR/3; % HT aspect ratio
Cl_alfa = 6.108; % HT airfoil lift curve slope (1/rad) CL_alfa_w = 4.827578; % Wing lift curve slope (1/rad) iw = 2.8; % Wing setting angle (deg)
alfa_sw = 13; % Wing airfoil stall angle (deg) alfa_fus = 0; % Fuselage AOA at cruise (rad)
alfa_sh = 10; % HT airfoil stall AOA (deg)

l_opt = Kc *sqrt(4*MAC*S*VH/(3.142*Df))% optimum tail arm (m) l = l_opt;
L = l/lL
Sh = VH*MAC*S/l % Horizontal tail area (m^2)
Cmo_wf= (Cm_af*AR*(cosd(swp)^2)/(AR+(2*cosd(swp)^2)))+(0.01*alfa_twist) % Wing/fuselage aerodynamic pitching moment coefficient
x=hc;
x0=0; y0=1;
x1=305; y1=0.9711;
x2=610; y2=0.9428;
L0=((x-x1)*(x-x2))/((x0-x1)*(x0-x2)); L1=((x-x0)*(x-x2))/((x1-x0)*(x1-x2)); L2=((x-x0)*(x-x1))/((x2-x0)*(x2-x1)); y=(L0*y0)+(L1*y1)+(L2*y2);
rho_c=y*1.225; % Air density at cruise altitude (kg/m^3) CLc=2*Wavg/(rho_c*S*Vc^2) % Aircraft cruise lift coefficient
CLh = (Cmo_wf+(CLc*(h-ho)))/(nh*VH) % Horizontal tail required CL at cruise CL_alfa_h = Cl_alfa/(1+(Cl_alfa/(3.142*ARh))) % HT lift curve slope (1/rad) set_h = CLh/CL_alfa_h % Initial HT setting angle (rad)
eo = 2*CLc/(3.142*AR) % Downwash angle at zero angle of attack (rad) e_slope = (2*CL_alfa_w)/(3.142*AR) % Downwash slope (rad/rad)
E = eo+(e_slope*(iw/57.3)) % Downwash angle at tail (rad)
bh = sqrt(ARh*Sh) % HT span
MACh = bh/ARh % HT MAC
Ch_root =3*MACh/(2*((1+lambdah+(lambdah^2))/(1+lambdah))) % HT root chord Ch_tip = lambdah * Ch_root % HT tip chord
ih = set_h-alfa_fus+E % HT setting angle (rad)

% Calculation of HT CL with lifting line theory N = 9; % (number of segments-1)
alpha_twist = 0.00001; % Twist angle (deg)
a_h = -5.12; % tail angle of attack (deg)
a_2d = Cl_alfa; % tail airfoil lift curve slope (1/rad)
alpha_0 = 0; % Airfoil zero-lift angle of attack (deg)
theta = pi/(2*N):pi/(2*N):pi/2; alpha=a_h+alpha_twist:-alpha_twist/(N-1):a_h;% segment’s angle of attack
z = (bh/2)*cos(theta);
c = Ch_root * (1 - (1-lambdah)*cos(theta)); % Mean Aerodynamics chord at each segment
mu = c * a_2d / (4 * bh);
LHS = mu .* (alpha-alpha_0)/57.3; % Left Hand Side
% Solving N equations to find coefficients A(i):
for i=1:N
for j=1:N
B(i,j)=sin((2*j-1) * theta(i)) * (1+(mu(i) *(2*j-1))/sin(theta(i))); end
end
A=B\transpose(LHS);
for i = 1:N
sum1(i) = 0;
sum2(i) = 0;
for j=1:N
sum1(i) = sum1(i) + (2*j-1) * A(j)*sin((2*j-1)*theta(i)); sum2(i) = sum2(i) + A(j)*sin((2*j-1)*theta(i));
end
end
CL_htail = pi * ARh * A(1)

set_h = a_h; % HT setting angle (deg) from lifting line theory
ih = set_h-alfa_fus+(E*57.3) % HT setting angle (deg)
HT_stall_AOA = alfa_sh-ih % Fuselage AOA for HT to stall (deg)
hnp = (1/4)+((1+(2/AR))/(1+(2/ARh))*(1-(4/(AR+2)))*VH); % Neutral point to chord ratio
Xcg = h*MAC; % CG distance (m) from Wing LE towards TE
SM = hnp-h % Static Margin
HT_Wing_area = Sh/S; % HT to wing area ratio
Cm_alfa = (CL_alfa_w *(h-ho))-(CL_alfa_h*nh*(Sh/S)*((l/MAC)-h)*(1-e_slope))% Longitudinal static stability derivative (1/rad)
ht_above = l*tand(alfa_sw-iw+3); % HT location above wing (m) for HT with higher vertical location relative to the wing ac
ht_below = l*tand(alfa_sw-iw-3) % HT location below wing (m) for HT with lower vertical location relative to the wing ac

HORIZONTAL TAIL DESIGN RESULT

1. Horizontal tail location: aft tail.
2. Horizontal tail volume coefficient: 0.3
3. Optimum arm: 0.3773m
4. Fuselage length: 0.6288m
5. Horizontal tail area: 0.0245m²
6. Wing/fuselage aerodynamic pitching moment coefficient: -0.0770
7. Horizontal tail desired lift coefficient: -0.3740
8. Horizontal tail airfoil section: NACA 0010
9. No sweep angle and no dihedral angle
10. Aspect ratio: 4.6667
11. Taper ratio: 0.7
12. Lift curve slope: 4.3118 rad⁻¹
13. Span: 0.3381m
14. Root chord: 0.0844m
15. Tip chord: 0.0590m
16. MACh: 0.0724m
17. Horizontal tail incidence: -1.39deg
18. Static Margin, SM: 0.2
19. Horizontal tail vertical location (relative to wing), ht < 0.0477m
20. Horizontal distance from wing root leading edge to tail root leading edge: 38.82cm
21. Horizontal distance from wing root leading edge to tail root trailing edge: 47.26cm

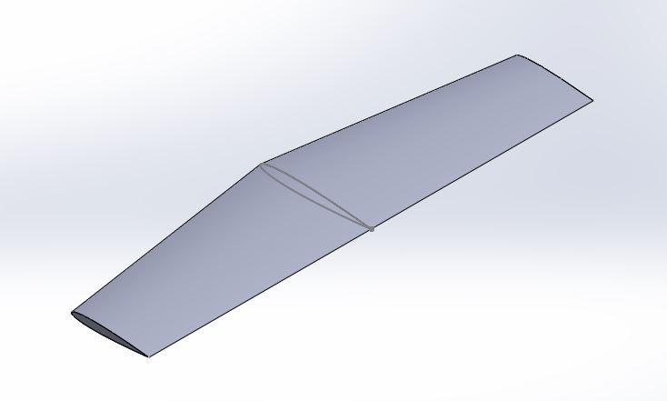
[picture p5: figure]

VETRTICAL TAIL DESIGN
The third lifting surface in a conventional aircraft is the vertical tail, which is sometimes referred to as a vertical stabilizer or fin. The vertical tail tends to have two primary functions: (i) directional stability and (ii) directional trim. The vertical tail will be designed to meet these two requirements. The vertical tail is a major contributor in maintaining directional control, which is the primary function of the rudder.
STEP 25: Vertical Tail Configuration: Conventional
STEP 25: Vertical Tail Volume Coefficient

Considering the effects, the vertical tail volume coefficient was selected to be 0.035.

STEP 26: Vertical Tail Moment Arm (lv)

This was select to be the same as the horizontal tail arm which is 0.3773m.

STEP 27: Vertical Tail Planform Area, SV

SV =

S∙b∙VV
lV

(6.33)

Figure 6.1: Designed horizontal tail in isometric view

SV =

0.1878 ∙ 1.1466 ∙ 0.035
0.3773 | = 0.02m²
STEP 28: Vertical Tail Airfoil Section

The vertical tail airfoil section was selected to be NACA 008 which has the following properties:

1. Zero-lift angle of attack (αo) is zero
2. Stall angle of attack is 8deg
3. Lift curve slope is 6.0176 1/rad
4. Ideal lift coefficient (Cli) is 0
5. Maximum Thickness to chord ((t/C)max) is 8%
6. Clmax is 0.77
7. Cdmin is 0.00958
8. Minimum Pitching moment is -0.009
9. Maximum (L/D) is 38.77
STEP 29: Vertical Tail Aspect Ratio, ARV

Considering the effects of vertical tail aspect ratio, it was selected to be 1.5. As a guideline, it was suggested (in Ref 1) that vertical tail aspect ratio should be between 1 and 2

STEP 30: Vertical Tail Taper Ratio: The vertical tail taper ratio was selected to be 0.75
STEP 31: Vertical Tail Incidence Angle: The vertical tail incidence was set to be zero.
STEP 32: Vertical Tail Sweep: no sweep angle
STEP 33: Vertical Tail Dihedral: no dihedral angle.
STEP 34: Vertical Tail Span, Root Chord, Tip Chord and MAC

To calculate the above tail parameters:

ARV =

bV
CV

(6.34)

λV =

cVtip

CVroot

(6.35)

CV =

2
3

CVroot (

1+λV+λV

2

1+λV

) | (6.36)

ARV =

bV

2

SV

(6.37)

Therefore:

1.5 =

bV

2
0.02

∴ bV = 0.173m

CV =

bV
ARV

=

0.173
1.5

= 0.115m

0.115 =

2
3

CVroot (

1 + 0.75 + 0.75²
1 + 0.75 ) ∴ CVroot = 0.131m

cVtip = λV∙CVroot = 0.75 × 0.131 = 0.0983m

STEP 35: Spin Recovery

Since this aircraft is not designed to be spinnable, spin recovery will not be considered.

STEP 36: Directional Trim

Since the aircraft is designed to be right-left symmetric, the directional trim equation is:

∑ Ncg = 0 ⇒ T ∙ Y + Lvlvt = 0 | (6.38)

Where T denotes the engine thrust, Y is the distance between the thrust line and the aircraft cg in the xy plane, lvt is the distance between the vertical tail aerodynamic center and the aircraft cg. LV is the horizontal tail lift.

The value for Y is zero because the center of gravity is to be at the center (since the aircraft is right-left symmetric) and the engine will be at the nose center.

The value for LV is also zero because the airfoil zero lift angle of attack is zero and the tail incidence is also zero. Therefore, vertical tail generated lift coefficient is zero which also makes the lift force to be zero.

∑Ncg = 0 ⇒ T ∙ 0 + 0 ∙ lvt = 0

STEP 37: Directional Stability

Cnβ = Kf1

- CLα_V

(1 −

dσ
dβ) ηv ∙
lvtSv bS | (6.39)

Where Cnβ is the directional stability, Kf is the fuselage contribution to directional stability, CLα_v is the vertical tail lift curve slope (in rad⁻¹

), ηv is vertical tail efficiency, dσ | dβ is the vertical tail side

wash gradient (in rad) and lvtSv
bS

is vertical tail volume coefficient.

The typical value for Kf1 ranges from 0.65 to 0.85 and was selected to be 0.75. Sidewash gradient was selected to be -2.6. The vertical tail efficiency was selected to be 0.9 (90%) tail volume coefficient has been selected earlier to be 0.035. vertical tail lift curve slope was calculated as:

CL∝_v =

dCLv
dαv

=

Cl∝_v

1+

Cl∝_v
π∙ARv

(6.40)

CL∝v

=

6.0176

1 +

6.0176
π ∙ 1.5

= 2.66rad⁻¹

Cnβ = 0.75 × 2.66 × (1 − (−2.6)) × 0.9 × 0.035 = 0.226rad⁻¹

VERTICAL TAIL DESIGN RESULT

1. Tail configuration: conventional
2. Vertical tail volume coefficient: 0.035
3. Vertical tail arm: 0.3773
4. Vertical tail area: 0.02m²
5. Airfoil section: Naca 0008
6. Vertical tail aspect ratio: 1.5
7. Vertical tail taper ratio: 0.75
8. Vertical tail incidence: 0ᵒ
9. No sweep and dihedral angle
10. Vertical tail span: 0.173m
11. Vertical tail MAC: 0.115m
12. Vertical tail root chord: 0.131m
13. Vertical tail tip chord: 0.0983m
14. Horizontal distance between wing LE to vertical tail LE: 37.355cm
15. Horizontal distance between wing LE to vertical tail TE: 50.455cm

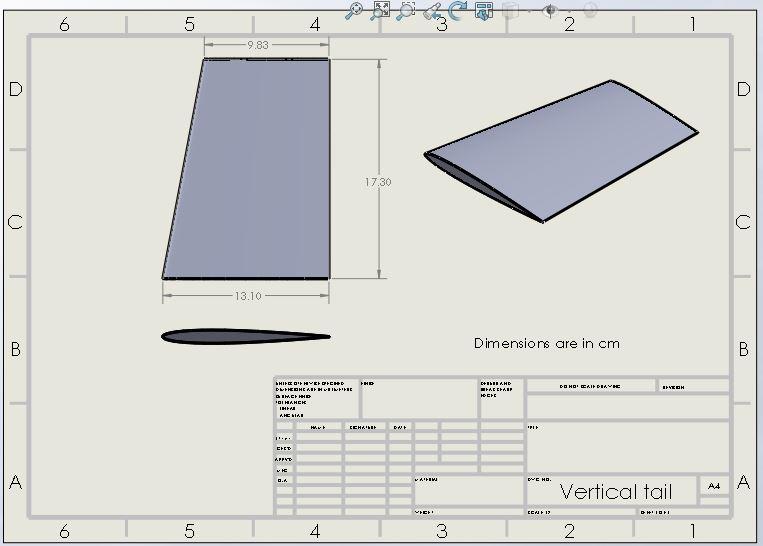
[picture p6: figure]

Figure 6.2: Designed vertical tail

# CHAPTER 7

FUSELAGE DESIGN
This design is a UAV which will carry a light payload (as light as a sweet or a chew gum). The payload is to be contained by the fuselage. Other components which are to be accommodated by the fuselage are batteries, receiver, switch, servo, wing and engine.

The fuselage was designed to accommodate all of these and this report encompasses a step-wise description of the procedures.

STEP 1: Design Requirement
I. Light weight
II. | Low drag
III. | Ease of manufacture
IV. | Accommodation of all internal components
V. Accommodation of the engine and the lifting surfaces VI. Give room for required tail arm

Type: low speed, single engine, prop-driven aircraft.

Payload: 10g sweet

STEP 2: Number of Crew Members – Nil
STEP 3: Number of Flight Attendant – Nil
STEP 4: Number of Technical Personnel – Nil
STEP 5: Human Size and Target Passenger – Nil
STEP 6: Fuselage Layout (Internal) Configuration

The following are to be accommodated by the fuselage:

I. Engine (Nose)
II. | Payload (Cabin)
III. | Battery (Cabin)
IV. | Receiver (Cabin)
V. Switch (Cabin)
VI. | Servo (Cabin)
VII. | Wing (Cabin top)
VIII. | Tails (aft fuselage)

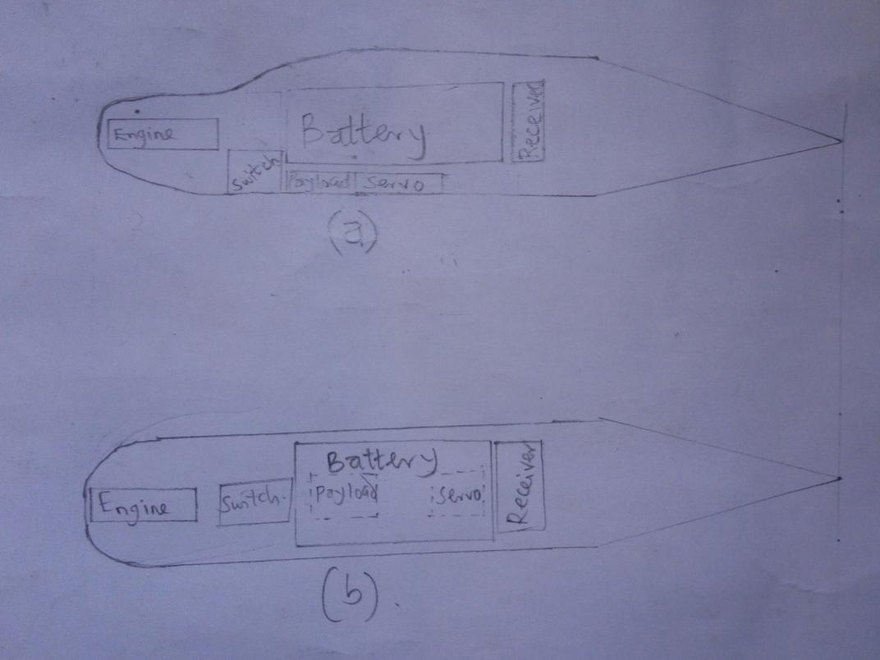
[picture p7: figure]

STEP 7: Cockpit Instrument – Nil
STEP 8: Cockpit Design

Since this is a UAV, there is no special design for the cockpit. Rather, it was designed alongside the nose.

STEP 9: Optimum Length to Diameter Ratio (LF/DF)opt

Considering the zero-lift drag coefficient, surface area and light weight, the fuselage length-to-diameter ratio was selected to be 6.

STEP 10: Cabin Design

As stated in step 6, the components in the cabin are: battery, payload, receiver, switch and servo. The component with the highest size (dimension) is the battery and was used to define the cabin configuration.

Cabin Width (WC)

The battery width is about 4.5cm. To hold the battery down to the fuselage, a space of 1.5cm was dedicated which makes the cabin width to be 6cm.

Figure 1: Sketch of fuselage configuration in (a) side view and (b) top view

Cabin Length (LC)

Battery length (LB) = 12cm, Receiver length (LR) = 5cm and Switch length (LS) = 5cm. The payload and servo will be embedded in the base wall.

LC = LB + LR + LS
(7.1)

LC = 12 + 5 + 5 = 22cm

Therefore, the cabin length is 22cm.

Cabin Height (HC)

The component with the highest height is the battery whose height is around 7cm. A tolerance of 1cm was left for holding the battery to the fuselage and to allow few wires. This made the cabin height to be 8cm.

STEP 11: Cargo/Load Compartment Design – Nil
STEP 12: Required Volume for Other Compartment – Nil
STEP 13: Space for Other Compartment – Nil
STEP 14: Fuselage Maximum Diameter (DF)

The proposed material for construction is Styrofoam with a thickness of 2cm. This implies that the wall thickness (TW) is 2cm.

Therefore, fuselage maximum width is 10cm (2TW + WC) and fuselage maximum height is 12cm (2TW + HC).

STEP 15: Number of Doors – two (cockpit windshield and aft fuselage)
STEP 16: Fuselage Nose Section

The fuselage nose length to maximum fuselage diameter ratio (LN/DF) should be between 1.5 and 2 and was selected to be 1.75. This makes the nose length to be 21cm.

As stated earlier, the nose is meant to accommodate the engine. To do this and insure ease of manufacturing, the nose section of the fuselage was designed as shown below.

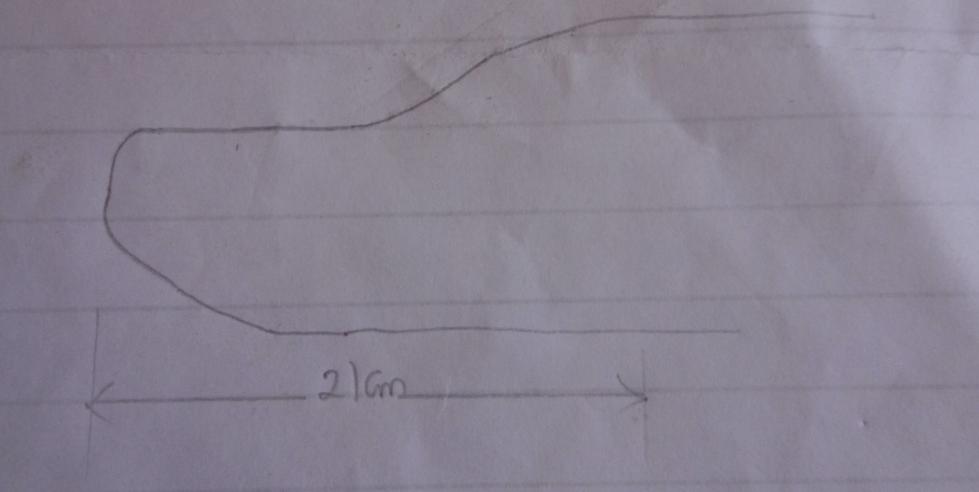
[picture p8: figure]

STEP 17: FUSELAGE REAR SECTION

As recommendation, the fuselage is desired to follow an airfoil shape to reduce drag. From top view, it is desired to be symmetric airfoil shape. To achieve this, the tail section was tapered to zero diameter (from top view) to form a cone-like shape. To avoid flow separation, the cone angle was selected to be as small as 12deg.

tan(αcone) =

WF/2
LR

(7.2)

LR =

WF/2
tan(αcone)

=

10/2
tan12 = 23.5cm
STEP 18: UPSWEEP ANGLE

For takeoff clearance, during takeoff rotation about the main landing gear (tricycle gear configuration), the fuselage aft section was expected not to touch the ground under normal flight operation and the upsweep angle was recommended to be less than 20deg (as seen from side view). The horizontal tail is to be mounted at the aft fuselage section and was designed to be some centimeters below the wing vertical location. To get this achieved, total upsweep wasn’t employed and the same approach as step 17 was used. For the fuselage rear section (from side view) to have the same length as in step 17, the upsweep angle was calculated as:

tan(αus) =

DF/2
LR

(7.3)

(αus) = tan⁻¹ (

DF/2
LR

) = tan⁻¹ (

12/2
23.5

) = 14.3deg

Since the upsweep angle is less than 20deg, it was left unaltered.

Figure 7.1: Sketch of fuselage nose section

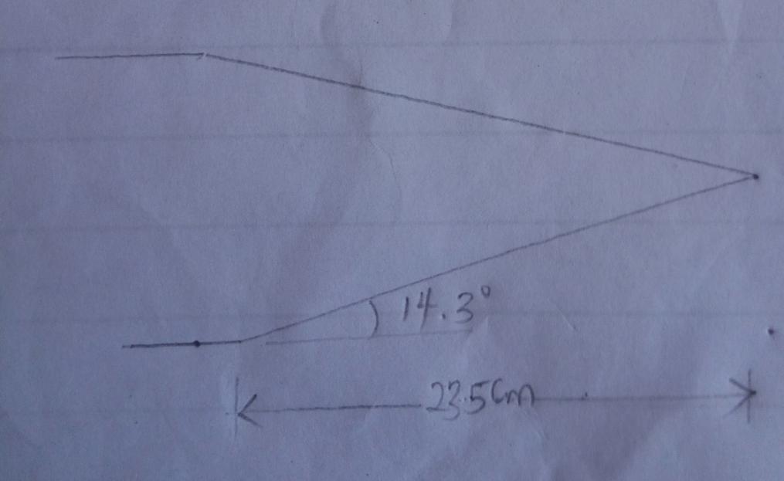
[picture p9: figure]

STEP 19: Fuselage Overall Length (LF)
LF = LN + LC + LR = 21 + 22 + 23.5 = 66.5cm | (7.4)
STEP 20: Check for Design Requirement Satisfaction

The fuselage length is 66.5cm and the maximum diameter is 12cm. Considering the horizontal distance between wing root leading edge and horizontal tail trailing edge (47.26cm), there is no sufficient space for the wing on the fuselage (cabin). Therefore, this design requirement is not satisfied.

To satisfy the requirement and to give room for other components positioning to put the aircraft center of gravity (CG) in the selected position, cabin length was increased by 10cm which increases the fuselage length to 76.5cm.

With this, the fuselage length-to-diameter ratio is 6.375 which is close to the selected value (i.e. 6).

Figure 7.2: Sketch of fuselage tail section

STEP 21: FUSELAGE DRAWING

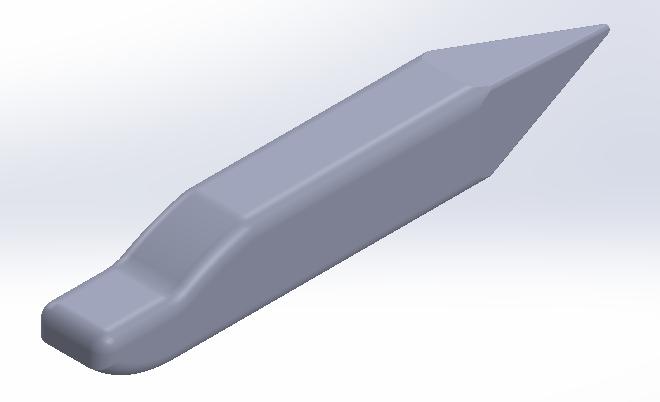
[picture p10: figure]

Figure 7.3: Fuselage final drawing

# CHAPTER 8

PROPULSION SYSTEM DESIGN
The propulsion system was expected to produce a maximum power of 22.7W and the propeller efficiency was expected to be around 85%. Below are the design steps taken in designing the propulsion system.
STEP 1: Design Requirements
1. Aircraft performance (speeds)
2. Engine cost
3. Operating cost
4. Engine efficiency
5. Maintainability
6. Engine weight
7. Aircraft stability
8. Noise and vibration
STEP 2: Engine Type

To satisfy the requirements stated above, especially engine weight, engine cost and operating cost, the engine type was selected to be electric motor. The reasons being that it is light in weight, low cost and no special operating cost (since the engine will be using a rechargeable battery).

STEP 3: Numbers of Engine – One.
STEP 4: Engine Location

Since there’s only a single engine, the options are for the aircraft to be a tractor or a pusher. But the decision of being a tractor was made because of longitudinal stability and reduction of weight as there will be need to compensate for weight or make weight distribution tasking/challenging in order to make the aircraft longitudinally stable. Therefore, the engine will be buried in the fuselage nose.

STEP 5: Engine Selection

From remote controlled (RC) airplane store, an electric motor with a power of around 30W was selected which was inherently designed to be compatible with a propeller with a diameter of 10 inches (25.4cm) and pitch 4.5inches.

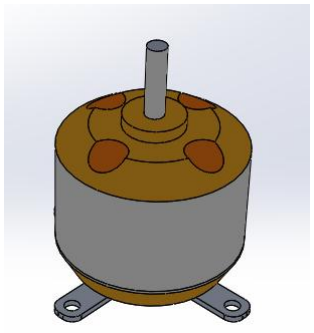
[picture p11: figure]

STEP 6: Propeller Design – There is an already design propeller for the selected electric motor.

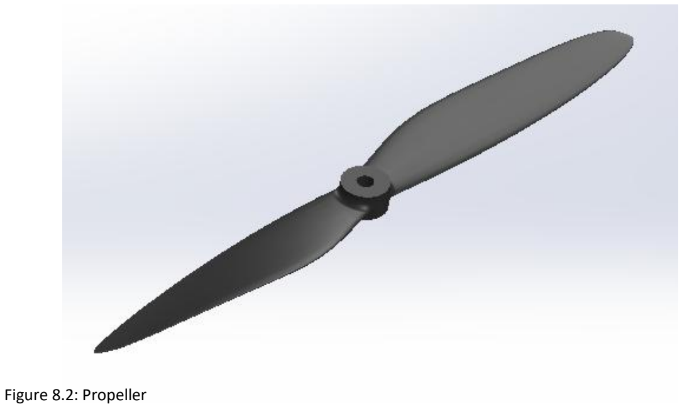
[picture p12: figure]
Figure 8.2: Propeller

STEP 7: Inlet Design – Nil

Figure 8.1: Electric motor

STEP 8: Engine Installation Design

Figure 8.3: Propeller – electric motor assembly

Figure 8.4: Engine – propeller assembly

# CHAPTER 9

LANDING GEAR DESIGN
The landing gear was designed to enable the aircraft to take-off and land safely on a concrete floor, carry the aircraft loads (static and dynamic) and other requirements that will be stated later in the process. The following parameters have been obtained during the earlier design phases and were employed in this section:
1. mTO = 1.2kg
2. Vs = 8m/s
3. K = 0.0551
4. S = 0,1878m²
5. Sh = 0.0245m²
6. Cmac_wf = -0.077
7. MAC = 0.164m
8. MACh: 0.0724m
9. CLTO = 1.1105
10. CLh = -0.374
11. Lh = 0.3773m
12. Xcg = 20% of MAC
13. Xac = 25%
14. CDo_TO = 0.0495
15. Dprop = 25.4cm
16. Pmax = 30W
17. ηpTO = 0.5
18. αfus_TO=5.27deg
19. μ (concrete floor)= 0.04
20. Iyy = 0.61kgm²
21. Takeoff pitch angular rate = 12deg/s²

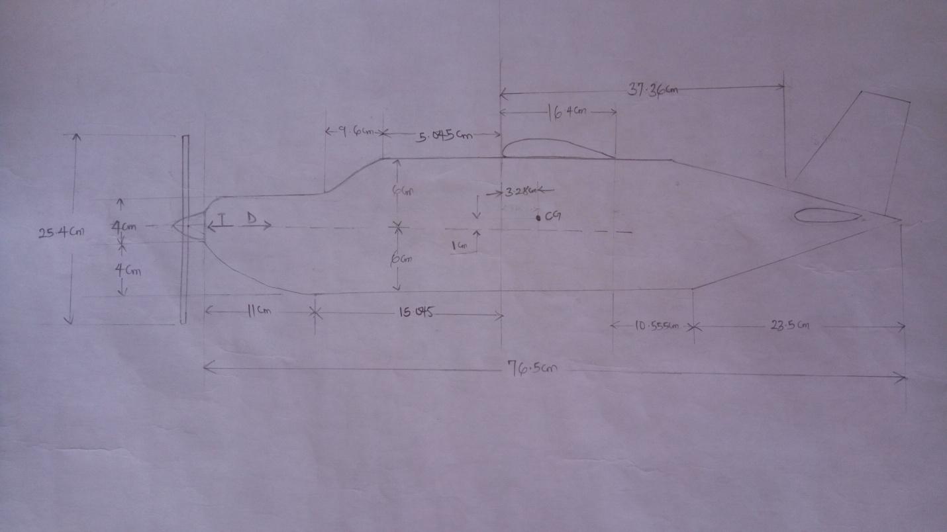
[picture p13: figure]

The following are the steps taken in landing gear design:

STEP 1: Design Requirement

The following are the design requirements that will be satisfied:

1. Ground clearance
2. Tipback angle
3. Takeoff rotation
4. Overturn angle
5. Aircraft ground stability
6. Aircraft ground controllability
7. Low cost
8. Maintainability
9. Manufacturability
STEP 2: Landing Gear Configuration – Tricycle
STEP 3: Landing Gear Type – Fixed
STEP 4: Fixed Type: Unfaired

Figure 9.1: Fuselage/Engine sketch with dimension

STEP 5: Aircraft Forward and Aft Center of Gravity (Cg) Location

The aircraft CG is located at 20% of the wing MAC which gives a distance of 3.28cm from the wing leading edge (LE). The aircraft CG is constant thus; there is no difference in the forward and aft CG location.

STEP 5: Calculation of Landing Gear Height Based On Ground Clearance Requirements

As can be seen from the figure above, propeller tip is the lowest point on the aircraft. To ensure safety, a clearance (ΔHclear) of 15cm was specified for the prop tip. The distance between the CG and prop center (ΔCG) is 1cm, Propeller diameter is 10in (25.4cm).

∴ HCG = ∆Hclear +

Dprop
2
+ ∆CG | (9.1)

HCG = 15 +

25.4
2

+ 1 = 28.7cm

Therefore, the distance between the CG point and ground is 28.7cm. Then, the main gear was assumed to be attached to the fuselage where the distance between the CG and the fuselage base (hCG) is 7cm.

∴ HLG = HCG − ℎCG | (9.2)

HLG = 28.7 − 7 = 21.7cm

Therefore, landing gear height is 21.7cm. The fuselage attachment and landing gear height will be reviewed if they do not satisfy other requirements.

STEP 7: Calculation of the Distance between the Main Gear and the Most Forward CG Position

The CG position is constant as stated earlier and is at an horizontal distance of 3.28cm from the wing LE

The maximum allowable distance between the main gear and the CG was obtained by considering the tree equilibrium governing equations of an aircraft which was simplified as:

xmg =

Iyymgθ−D(ZD−Zmg)+T(ZT−Zmg)−Macwf−ma(Zcg−Zmg)−W∙xcg+Lwfxacwf+Lℎxacℎ

Lwf+Lℎ−W
(9.3)

Each of the parameters in the equation above was obtained one after the other and was then substituted into the equation.

CDTO = CDOTO

+ K ∙ CLTO

2
(9.4)

CDTO = 0.0495 + 0.0551 ∙ 1.1105² = 0.1174

D =

1
2

ρVR

2CDTOS | (9.5)

VR = 1.1VS = 1.1 × 8 = 8.8m/s

Where VR is the aircraft linear forward speed at the instant of rotation.

D =

1
2
- 1.225 ∙ 8.8

2
- 0.1174 ∙ 0.1878 = 1.046N

T =

ηPTO×Pmax
VR
| (9.6)

T =

0.5 × 30
8.8

= 1.7045N

Macwf =

1
2

ρVR

2SCmacwf
C | (9.7)

Macwf =

1
2

× 1.225 × 8.8

2 × 0.1878 × (−0.077) × 0.164 = −0.1125N ∙ m

From the first equilibrium equation, this was obtained:

a =

T−D−Ff
m

(9.8)

Ff = μN | (9.9)
N = W − LTO | (9.10)

LTO =

1
2

ρVR

2CLTOS | (9.11)

LTO =

1
2
- 1.225 ∙ 8.8

2
- 1.1105 ∙ 0.1878 = 9.892N

N = (1.2 × 9.81) − 9.892 = 1.88N

Ff = 0.04 × 1.88 = 0.0752N

a =

1.7045 − 1.046 − 0.0752
1.2

= 0.486m/s

Lℎ =

1
2

ρVR

2CLℎ
Sℎ | (9.12)

Lℎ =

1
2
- 1.225 ∙ 8.8

2
- (−0.374) ∙ 0.0245 = −0.4346N

Lwf = LTO − Lℎ | (9.13)

Lwf = 9.892 − (−0.4346) = 10.3266N

ZD – Zmg implies the distance between the Drag force point and the ground which is 27.7cm (6cm + 21.7cm).

ZT – Zmg implies the distance between the Drag force point and the ground which is 27.7cm (6cm + 21.7cm).

Zcg – Zmg implies the distance between the Drag force point and the ground which is 28.7cm (1cm + 6cm + 21.7cm). This has also been calculated earlier.

X distances are measured relative to a reference point. The reference here was chosen to be the aircraft CG for simplicity. Therefore, the distance between the wing/fuselage aerodynamic centre and cg (xacwf) was calculated as shown below since the wing is rectangular.

xacwf = (Xac − Xcg) × MAC | (9.14)

xacwf = (0.25 − 0.2) × 16.4 = 0.82cm

Horizontal tail aerodynamic center location (xacℎ
) is located on the tail MAC which has to be transferred to the root chord for easy reference to the wing leading edge.
xacℎ = lℎ + xacwf | (9.15)

xacℎ = 37.75 + 0.82 = 38.55cm

The reference point is the CG point therefore, xcg is zero.

xmg

=

0.61 ∙

12
57.3

− 1.046 ∙ (0.277) + 1.7045(0.277) − (−0.1125) − 1.2 ∙ 0.486(0.287) − 0 + (10.3266 ∙ 0.0082) + (−0.4346) ∙ 0.3855 10.3266 + (−0.4346) − (11.772) = 0.917m

In getting this value, the moment of inertia used is about the aircraft CG which has to be transferred to the main gear using parallel axis theorem and the xmg was recalculated with the new moment of inertia value.

Ixxmg = Ixxcg

+ m (√xmg
2 + HCG

2

)

2
(9.16)

Ixxmg = 0.61 + 1.2(0.0917² + 0.287² ) = 0.72

xmg

=

0.72 ∙

12
57.3

− 1.045 ∙ (0.277) + 1.7045(0.277) − (−0.1125) − 1.2 ∙ 0.4869(0.287) − 0 + (10.3266 ∙ 0.0082) + (−0.4346) ∙ 0.3855 10.3266 + (−0.4346) − (11.772) = 0.1181m

The maximum distance from the CG and the main gear is 11.81cm. This value is quite much and was reduced to 6.5cm.

STEP 8: Calculation of the Distance between the Main Gear and Most Aft CG

The aircraft CG position is constant. Therefore, Xcgaft = Xcgfor = 0.2MAC

STEP 9: Tipback Check

To prevent tipback during takeoff rotation, the tipback angle must be greater than the fuselage takeoff angle of attack by a minimum of 5deg.

αtb > αTO + 5 | (9.17)

αtb = tan⁻¹

(

xmgaft

HCG

) | (9.18)

Where Xmgaft = Xmgaft = 6.5cm and HCG has been calculated earlier to be 28.7cm

αtb = tan⁻¹ (

6.5
28.7

) = 12.76ᵒ

Tipback angle is greater than the aircraft takeoff rotation (5.27ᵒ)

αtb > 5.27 + 5

STEP 10: Takeoff Rotation Clearance Check

The take-off rotation ground clearance requirement to prevent a fuselage hit is as follows:

αC ≥ αTO | (9.19)

In order to determine the clearance angle (αc), the two distances required are (i) the main gear distance from the fuselage upsweep point (Xmg-us) and (ii) the distance between the fuselage lowest point and the ground (Hf).

xmg−LE = xmg + (Xcg × MAC) | (9.20)

xmg−LE = 6.5 + (0.2 × 16.4) = 9.78cm

xmg−us = xLE−us − xmg−LE | (9.21)

xmg−us = (16.4 + 10.555) − 9.78 = 17.175cm

Where xmg-LE is the distance between the main gear and wing LE; xLE-us is the distance between the wing LE and the upsweep point; and xmg-us is the distance between the main gear and the upsweep point.

The distance between the fuselage lowest point and the floor (Hf) is the same as the landing gear height (21.7cm)

αC = tan⁻¹ (
Hf
xmg−us) | (9.22)

αC = tan⁻¹ (

21.7
17.175) = 51.64ᵒ

Since the clearance angle (αC = 51.64ᵒ) is greater than the takeoff rotation angle, the fuselage will not touch the ground.

STEP 11: Wheel Base Calculation

Based on ground controllability requirement, the nose gear is required not to carry less than about 5% of the total load and also not to carry more than about 20% of the total load. Thus, the main gear carries about 80 – 95% of the aircraft load. To meet this requirement, it was decided that the nose gear should carry 20% of the total load and the main gear 80% of the total load.

To calculate the wheel base, the following equilibrium equations were employed:

∑ Fz = 0 ; Fn + Fm = W | (9.23)
∑ Mo = 0 ; FnB − WBm = 0 | (9.24)

∴ Fn =

Bm
B
W | (9.25)

Fm =

Bn
B
W | (9.26)

Where, Fn and Fm are the static loads carried by the nose gear and main gear respectively, Bn and Bm are the distances from the nose gear and main gear to the CG respectively, B is the wheel base (distance between the main gear and the nose gear along the x-axis) and W is the aircraft weight.

The nose gear was said to carry 20% of the load (i.e. Fn = 0.2W) and Bm is the same as xmg (6.5cm).

Equation 24 can be rewritten as:

B =

Bm
Fn

W =

Bm
0.2W

W =

6.5
0.2
= 32.5cm | (9.27)

Therefore, the wheel base is 32.5cm.

STEP 12: WHEEL TRACK CALCULATION

The three main design requirements which drive the wheel track, T, (distance between the wheels of the main gear along the lateral axis) are: (i) ground lateral control, (ii) ground lateral stability, and (iii) structural integrity. The overturn angle is the angle which is critical to the aircraft overturn.

The lateral distance between each main gear to the cg must be greater than 25 deg. Hence, 30deg was considered. The minimum allowable value for wheel track was calculated as:

tan(30) =

Tmin⁄2

HCG

| (9.28)

Tmin = 2tan(30) × HCG = 2tan(30) × 28.7 = 33.14cm

GROUND CONTROLLABILITY

This was considered so that the aircraft will not roll over during taxi. The force that can roll the aircraft over is the centrifugal force (FC) which is created during a turn due to centripetal acceleration:

FC =

mV

2

R

| (9.29)

Where V is the speed and R is the turn radius. The speed and turn radius were selected to be 6m/s and 7m respectively.

FC =

1.2 × 6

2
7

= 6.17N

The restoring moment of the aircraft weight is a function of the wheel track:

TGC > 2

FC∙HCG
mg
| (9.30)

TGC > 2 ×

6.17 × 28.7
1.2 × 9.81 > 30.08cm

The corresponding overturn angle is given as:

φot > tan⁻¹

(

FC
mg) | (9.31)

φot > tan⁻¹ (

6.17
1.2 × 9.81) = 27.66ᵒ

Therefore, based on ground controllability, the wheel track should be greater than 30.08cm with a corresponding overturn angle greater than 27.66ᵒ

GROUND STABILITY

The consideration of ground stability is based on generation of restoring moment to balance the forces on an aircraft at ground created by crosswind. The cross-wind force (FW) on an aircraft may be modeled as a drag force and is calculated as follows:

FW =

1
2

ρVw

2AsCDs
(9.32)

Where VW represents the wind speed, and AS represents the aircraft side area. The parameter CDS is called the aircraft side drag coefficient and its value varies between 0.3 and 0.8.

CDS was selected to be 0.55, Vw was assumed to be 20m/s and with the aid of solidworks, AS was obtained to be 0.05m²

FW =

1
2

× 1.225 × 20² × 0.05 × 0.55 = 6.7375N

The wheel track for ground stability I given as:

TGS > 2

FW∙HC
W

(9.33)

Where, HC is the centroid height from the ground. The centroid is 7cm above the fuselage base. Therefore, HC is 28.7cm (7cm + 21.7cm).

TGS > 2 ×

6.7375 × 28.7
11.772 > 32.85cm

Therefore, the wheel track based on ground stability should be greater than 32.85cm.

STEP 13: LANDING GEAR ATTACHMENT

Landing gear attachment has been stated earlier to be under the fuselage and it satisfies all requirements. The wheel base can be achieved with this attachment. Also the wheel height will make it easy to achieve the wheel track.

STEP 14: CALCULATION OF LOADS ON EACH GEAR

The load carried by the landing gear is of two types: (i) static load and (ii) dynamic load. The calculation of landing gear load involves the two loads and was calculated as below:

Fnmax =

Bm
B
W | (9.34)

Fnmax =

6.65
32.5
- 11.772 = 2.409N

Therefore, the maximum nose gear static load is 2.409N

Fndyn =

W|aL|HCG
gB

(9.35)

Where, Fndyn is nose gear dynamic load, HCG is the CG height from ground and aL is the landing gear deceleration and was selected to be -0.5m/s²

Fndyn =

11.772 ∙ 0.5 ∙ 28.7
9.81 ∙ 32.5

= 0.5298N

Fmmax =

Bn
B
W | (9.36)

Where, Fmmax is the main gear maximum static load.

Bn = B − Bm | (9.37)

Bn = 32.5 − 6.5 = 26cm

Fmmax =

26
32.5
- 11.772 = 9.418N

Fmdyn =

WaTHCG
gB

(9.38)

Where, Fndyn is the main gear dynamic load and aT is the aircraft takeoff acceleration and was calculated in STEP 7 to be 0.486

Fmdyn =

11.772 ∙ 0.486 ∙ 28.7
9.81 ∙ 32.5

= 0.515N

The total load on each gear is the summation of both static and dynamic loads.

FN = Fnmax + Fndyn | (9.39)

FN = 2.409 + 0.5298 = 2.9388N

FM = Fmmax + Fmdyn | (9.40)

FM = 9.481 + 0.515 = 10N

Therefore, the total loads carried by the nose gear and the main gear are 2.9388N and 10N respectively.

LANDING GEAR DESIGN RESULTS

1. Landing gear configuration – Tricycle
2. Landing gear type – Fixed
3. Aircraft CG location – 3.28cm from wing LE
4. CG height from ground – 28.7cm
5. Landing gear height from ground – 21.7cm
6. Main gear distance from CG – 6.5cm
7. Tipback angle – 12.76ᵒ
8. Takeoff rotation clearance – 51.64cm
9. Wheel base – 32.5cm
10. Minimum wheel track – 33.14cm
11. Wheel track based on ground controllability > 30.08cm
12. Overturn angle – 27.66ᵒ
13. Wheel track based on ground stability > 32.85cm
14. Landing gear attachment – under fuselage
15. Nose gear load – 2.9388N
16. Main gear load – 10N

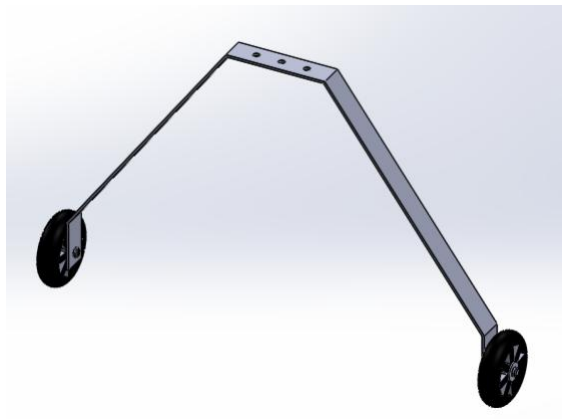
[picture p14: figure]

Figure 9.2: Main gear drawing

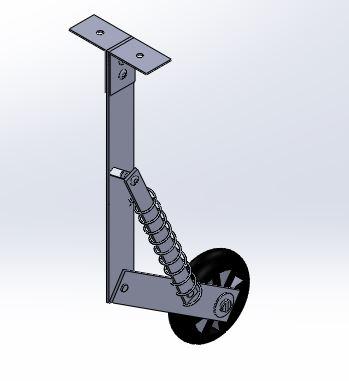
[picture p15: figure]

Figure 9.3: Nose gear drawing

# CHAPTER 10

WEIGHT OF COMPONENTS
The weight of the components for this design was divided into:
1. Fuselage weight
2. Wing weight
3. Tail weight
4. Landing gear weight
5. Propulsion system weight
6. Payload and store weight
7. Others

The weight of the components was then analyzed using this division as guidelines. To obtain the weights, the density of the various materials to be used was obtained and volumes of each of the components were calculated. From these, the mass was obtained which was then converted to weight. The following are the steps taken.

FUSELAGE MASS

For ease in calculation of the fuselage volume, the views (side, top and bottom views) are divided into sections. This section form shapes assumed to be triangles and rectangle because they are similar to these shapes as shown in the figure below.

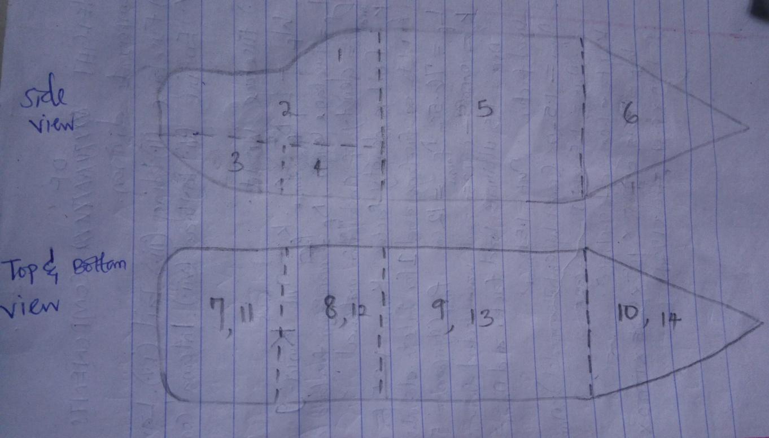
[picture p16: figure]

Figure 10.1: Fuselage sections sketch

The dimensions for these sections were obtained from the figure below

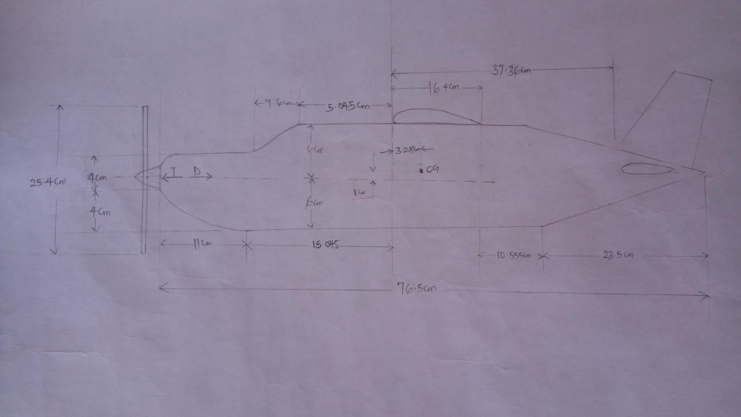
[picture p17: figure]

Sections 1 to 6, 7 to 10 and 11 to 14 are for side view, top view and bottom view. The two sides of the aircraft are symmetrical. The wall thickness is 2cm. This will affect the values to be used for fuselage width in sections 7 to 14.

Section 1: A1 =

1
2

× b × ℎ =

1
2

× 9.6 × 4 = 19.2cm²
(10.1)

Section 2: A2 = l × ℎ = 21 × 4 = 84cm² (10.2)

Section 3: A3 =

1
2

× b × ℎ =

1
2

× 11 × 4 = 22cm²

Section 4: A4 = l × ℎ = 10 × 4 = 40cm²

Section 5: A5 = l × ℎ = 32 × 12 = 384cm²

Section 6: This section was treated as two triangles. The actual horizontal length was gotten from the top view which is equivalent to the slant length as seen from top view.

Therefore, from Pythagoras theorem,

Figure 10.2: Aircraft sketch with dimension

b = √(
Fw
2

)

2
+ LR

2 = √(
10
2

)

2
+ 23.5
2 = 24.03cm | (10.3)

A6 = 2 × (

1
2

× b × ℎ) = 2 × (

1
2

× 24.03 ×

12
2

) = 144.18cm²

Section 7: A7 = l × w = 11 × (10 − 2 − 2) = 66cm²
| (10.4)

Section 8: From side view, it is seen that the length seen from top view is slant. So, Pythagoras theorem was used for the length.

A8 = l × w = √10² + 4
2 × (10 − 2 − 2) = 64.62cm²

Section 9: A9 = l × w = 32 × (10 − 2 − 2) = 192cm²

Section 10: In this section, the same approach used in section 6 was used to calculate the length.

l = √(
Fℎ
2

)

2
+ LR

2 = √(
12
2

)

2
+ 23.5
2 = 24.25cm | (10.5)

The sidewall thickness has taken part of the total geometry of this section as shown below.

Therefore, b = (

10
2

− 2) × tan(90 − αcone) = 3 × tan(90 − 12) = 14.114cm

A10 = 2 × (

1
2

× b × ℎ) = 2 × (
1
2

× 14.114 × (

10
2

− 2)) = 42.34cm²

Section 11: A11 = l × w = √11² + 4 2 × (10 − 2 − 2) = 70.23cm²

Figure 10.3: Aft fuselage sidewall thickness sketch

Section 12: A12 = l × w = 10 × (10 − 2 − 2) = 60cm²

Section 13: A13 = A9 = 192cm²

Section 14: A14 = A10 = 42.34cm²

Total Fuselage Area (Afus)

Afus = 2 ∑ Ai

6
i=1 | + ∑ | Ai

14
i=7

(10.6)

Afus = 2(19.2 + 84+ 22 + 40 +384 + 144.18)+ (66 + 64.62 + 192 + 42.34 + 70.23 + 60+ 192 + 42.34)

Afus = (2 × 693.38) + 729.53 = 2116.29cm²

Fuselage Volume (Vfus)

Vfus = Afus × Wall tℎickness | (10.7)

Vfus = 2116.29 × 2 = 4232.58cm³

Vfus = 4232.58 × 10⁻⁶m³ = 0.004233m³

Fuselage material is Styrofoam, with density of 50Kg/m³ .

mfus = ρfusmat

× Vfus | (10.8)

mfus = 50 × 0.004233 = 0.21165Kg or 211.65g

WING MASS

Wing compositions are:

i. Six ribs
ii. | One spar
iii. | Covering
iv. | Two ailerons
v. Two flaps
vi. Others (Servo, push-pull rod and miscellaneous)

Six Ribs

Parameters:

a. Airfoil section: Clark Y
b. MAC: 16.4cm c. Airfoil Maximum thickness to chord: 11.71%
d. MAC airfoil section area, Asection: 21.78cm²
e. Rib thickness, trib: 2cm
f. Rib material (Styrofoam) density: 50Kg/m³ Vrib = Asection × t = 21.78 × 2 = 43.56cm³ (10.9)
mrib = ρribmat × Vrib | (10.10)

mrib = 50 × 43.56 × 10⁻⁶ = 0.0022Kg

Six ribs mass = 6(0.0022) = 0.0132Kg (13.2g)

Spar

Parameters:

a. Spar thickness: 0.5cm
b. Height: 1.7cm
c. Spar length = 125cm (fuselage occupied space was considered)
d. Spar material density: 200Kg
Vspar = tspar × ℎspar × lspar = 0.5 × 1.7 × 125 = 106.25cm³ | (10.11)

mspar = ρsparmat

× Vspar | (10.12)

mspar = 200 × 106.25 × 10⁻⁶ = 0.02125Kg

Spar mass = 0.02125Kg (21.25g)

Covering

Parameters:

a. Wing span: 125cm (adding fuselage width to wetted span)
b. MAC airfoil section arc length: 33.52cm
c. Covering material density: 100Kg/m³
d. Covering thickness: 0.2cm
Vcov = Scov × lcov × tcov = 125 × 33.52 × 0.2 = 838cm³ | (10.13)
mcov = ρcovmat × Vcov | (10.14)

mcov = 100 × 838 × 10⁻⁶ = 0.0838Kg

Covering mass =0.0838Kg (83.8g)

Two ailerons

The two ailerons mass is assumed to be 10% of rib, spar and covering mass.

∴ mail = mrib + mspar + mcov | (10.15)

mail = 0.1 × (0.0132 + 0.02125 + 0.0838) = 0.1(0.11825) = 0.011825Kg

Ailerons mass = 0.011825Kg (11.83g)

Two flaps

The two flaps mass is assumed to be 15% of rib, spar and covering masses.

∴ mflap = mrib + mspar + mcov | (10.16)

mail = 0.15 × (0.0132 + 0.02125 + 0.0838) = 0.15(0.11825) = 0.01774Kg

Flaps mass = 0.01774Kg (17.74g)

Others

A servo mass = 9g. Therefore, 4servos =36g

A push-pull rod mass = 4g, 4 push-pull rods = 16g

Miscellaneous 10g

Total others mass =62g (0.062Kg)

TOTAL WING MASS, mwing = 0.01320 + 0.02125 + 0.0838 + 0.011825 + 0.01774 + 0.062 = 0.2098Kg

TAIL MASS

Horizontal Tail Mass

Horizontal tail compositions are:

i. Five ribs
ii. | One spar
iii. | Covering
iv. | Elevator

v. Others (Servo, push-pull rod and miscellaneous)

Five Ribs

Parameters:

a. Airfoil section: NACA 0010
b. MAC: 7.24cm
c. Airfoil Maximum thickness to chord: 10%
d. MAC airfoil section area, Asection: 3.59cm²
e. Rib thickness, trib: 1cm
f. Rib material (styrofoam) density: 50Kg/m³ Vrib = Asection × t = 3.59 × 1 = 3.59cm³
(10.17)
mrib = ρribmat × Vrib | (10.18)

mrib = 50 × 3.59 × 10⁻⁶ = 0.0001795Kg

Five ribs mass = 5(0.0001795) = 0.0008975Kg (0.9g)

Spar

Parameters:

a. Spar thickness: 0.5cm
b. Height: 0.6cm
c. Spar length = 33.8cm
d. Spar material density: 200Kg
Vspar = tspar × ℎspar × lspar = 0.5 × 0.6 × 33.8 = 10.14cm³ | (10.19)

mspar = ρsparmat

× Vspar | (10.20)

mspar = 200 × 10.14 × 10⁻⁶ = 0.002028Kg

Spar mass = 0.002028Kg (2.03g)

Covering

Parameters:

a. Horizontal tail area: 0.0245m²
b. MAC: 7.24cm
c. Covering span: 33.84cm (area/MAC)
d. MAC airfoil section arc length: 14.71cm e. Covering material density: 100Kg/m³
f. Covering thickness: 0.2cm
Vcov = Scov × lcov × tcov = 33.84 × 14.71 × 0.2 = 99.56cm³ (10.21)
mcov = ρcovmat × Vcov | (10.22)

mcov = 100 × 99.56 × 10⁻⁶ = 0.009956Kg

Covering mass =0.009956Kg (9.96g)

Elevator

The elevator mass is assumed to be 20% of rib, spar and covering mass.

∴ mele = mrib + mspar + mcov | (10.23)

mail = 0.2 × (0.0008975 + 0.002028 + 0.009956) = 0.2(0.0128815) = 0.0025763Kg

Elevator mass = 0.0026Kg (2.6g)

Others

A servo mass = 9g, 2servos =18g

A push-pull rod mass = 4g, 2 push-pull rods = 8g

Miscellaneous = 5g

Total others mass =31g (0.031Kg)

TOTAL HORIZONTAL TAIL MASS, mHT = 0.0008975 + 0.002028 + 0.009956 + 0.0026 + 0.031 = 0.0464815Kg

Vertical Tail Mass

Vertical tail compositions are:

i. Four ribs
ii. | One spar
iii. | Covering
iv. | Rudder
v. Others (Servo, push-pull rod and miscellaneous)

Four Ribs Parameters:

a. Airfoil section: NACA 0008

b. MAC: 11.5cm
c. Airfoil Maximum thickness to chord: 8%
d. MAC airfoil section area, Asection: 7.26cm²
e. Rib thickness, trib: 1cm
f. Rib material (styrofoam) density: 50Kg/m³ Vrib = Asection × t = 7.26 × 1 = 7.26cm³
(10.24)
mrib = ρribmat × Vrib | (10.25)

mrib = 50 × 7.26 × 10⁻⁶ = 0.000363Kg

Four ribs mass = 4(0.000363) = 0.001452Kg (1.45g)

Spar

Parameters:

a. Spar thickness: 0.4cm
b. Height: 0.5cm
c. Spar length = 17.3cm
d. Spar material density: 200Kg
Vspar = tspar × ℎspar × lspar = 0.4 × 0.5 × 17.3 = 3.46cm³ | (10.26)

mspar = ρsparmat

× Vspar | (10.27)

mspar = 200 × 3.46 × 10⁻⁶ = 0.000692Kg

Spar mass = 0.000692Kg (0.7g)

Covering

Parameters:

a. Vertical tail area: 0.02m²
b. MAC: 11.5cm
c. Covering span: 17.4cm (area/MAC)
d. MAC airfoil section arc length: 23.23cm
e. Covering material density: 100Kg/m³
f. Covering thickness: 0.2cm
Vcov = Scov × lcov × tcov = 17.4 × 23.23 × 0.2 = 80.8404cm³ | (10.28)
mcov = ρcovmat × Vcov | (10.29)

mcov = 100 × 80.8404 × 10⁻⁶ = 0.00808404Kg

Covering mass =0.00808404Kg (8.08g)

Rudder

The rudder mass is assumed to be 20% of rib, spar and covering mass.

∴ mele = mrib + mspar + mcov | (10.30)

mail = 0.2 × (0.001452 + 0.000692 + 0.00808404) = 0.2(0.0102) = 0.002Kg

Elevator mass = 0.002Kg (2g)

Others

A servo mass = 9g

A push-pull rod mass = 4g

Miscellaneous = 5g

Total others mass =18g (0.018Kg)

TOTAL VERTICAL TAIL MASS, mVT = 0.001452 + 0.000692 + 0.00808404 + 0.002 + 0.018 = 0.0302Kg

TOTAL TAIL MASS, mtail = VERTICAL TAIL + HORIZONTAL TAIL = 0.0302 + 0.0464815 = 0.07668Kg

LANDING GEAR MASS

Landing strut material is aluminum with density of 2711Kg/m³

Nose Gear

Nose gear strut components:

i. Vertical components
ii. | Slant component
iii. | End-of-travel (E.O.T) rod/spring guide rod
iv. | Fuselage attachment

Vertical component

Length: 17.5cm, Breadth: 2cm and thickness: 2mm

Vvert = l × b × t = 17.5 × 2 × 0.2 = 7cm³ (10.31)

Slant component

Length: 11cm, Breadth: 2cm and thickness: 2mm

Vslant = l × b × t = 11 × 2 × 0.2 = 4.4cm³ (10.31)

E.O.T rod

Figure 10.4: Nose gear sketch with dimension

Length: 12cm, Breadth: 1cm and thickness: 2mm

VE.O.T. = l × b × t = 12 × 1 × 0.2 = 2.4cm³ (10.31)

Fuselage attachment

Length: 6cm, Breadth: 2cm and thickness: 1mm

Vfus = l × b × t = 6 × 2 × 0.1 = 1.2cm³ (10.31)

Total nose gear strut volume, VNGS = Vvert + Vslant + VE.O.T. + Vfus | (10.32)

VNGS = 7 + 4.4 + 2.4 + 1.2 = 15cm³

mNGS = ρNGSmat × VNGS | (10.33)

mNGS = 2711 × 15 × 10⁻⁶ = 0.040665Kg

Others

a. Spring mass = 15g
b. Tire = 25g
c. Bolts, nuts washers and rivets = 30g
d. Miscellaneous = 10g

Nose gear mass, mNG = 40.7 + 15 + 25 + 30 + 10 = 120.7g (0.1207Kg)

Main Gear

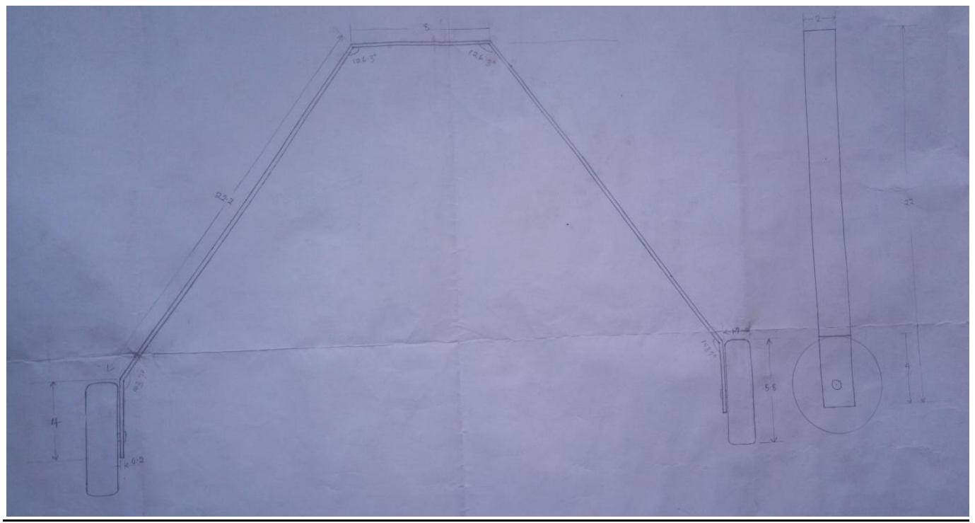
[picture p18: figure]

Figure 10.5: Main gear sketch with dimension

Strut parameters mass:

Thickness = 2mm, width = 2cm and Length = 2(4 + 22.2) + 8 = 60.4cm.

Vstrut = t × w × l = 0.2 × 2 × 60.4 = 24.16cm³

mstrut = ρstrutmat × Vstrut

mstrut = 2711 × 24.16 × 10⁻⁶ = 0.0655Kg

Others

a. Tire (2) = 50g
b. Bolts, nuts and washers = 35g
c. Miscellaneous = 15g

Main gear mass, mMG = 65.5 + 50 + 35 + 15 = 165.5g (0.1655Kg)

Landing gear mass, mLG = Nose gear mass + Main gear mass = 0.1207 + 0.1655 = 0.2862Kg

PROPULSION SYSTEM MASS

Electric motor = 47g, Propeller = 7.5g and Engine mount = 20g

Total mass, mPS = 47 + 7.5 + 20 = 74.5g (0.0745Kg)

STORE AND PAYLOAD MASS

i. Payload = 10g
ii. | Store casing 15g
iii. | Servo = 9g
iv. | push-pull rod = 4g

Total mass, ms = 10 + 15 + 9 + 4 = 38g (0.038Kg)

INTERNAL COMPONENTS AND OTHERS

i. Receiver = 8g
ii. | Battery = 240g
iii. | Electronic speed controller (ESC) = 23g
iv. | Lightening =30g
v. Wires = 30g
vi. Switch = 10g

Total mass, mint = 8 + 240 + 23 + 50 + 30 + 10 = 341g (0.361Kg)

Total aircraft mass, maircraft = mfus + mwing + mtail + mLG + mPS + mS + mint | (10.34)

maircraft = 211.65 + 209.8 + 76.68 + 286.2 + 74.5 + 38 + 341 = 1237.83g

Therefore, total mass = 1237.83g = 1.238Kg

Aircraft weight, Waircraft = maircraft × g = 1.238 × 9.81 = 12.14N | (10.35)

TOTAL AIRCRAFT WEIGHT = 12.14N

# CHAPTER 11

AIRCRAFT WEIGHT DISTRIBUTION
This section covers the calculation of aircraft center of gravity (CG) coordinates. To do this, the centers of gravity of each component were calculated and the distances from a reference point was considered. The details are discussed in the following steps:
STEP 1: Reference Line

The x-axis reference line is selected to be the prop spinner tip, y-axis reference is fuselage center line and z-axis reference line is the ground. The CG coordinate along the y-axis is assumed to be zero because the aircraft is designed to be right-left symmetric and the components are also distributed symmetrically. Therefore, only x and z axis are considered.

STEP 2: Coordinate Axis System – Body axis system
STEP 3: Wing Leading Edge Distance from Reference, XWLE-R

The wing leading edge is at a distance of 26.045cm from the fuselage nose and the spinner tip at a distance of 4cm from fuselage nose. Therefore, XWLE-R is 30.045cm.

STEP 4: Wing CG Coordinate

The wing CG (on x-axis) is assumed to be at 35% MAC and wing MAC is 16.4cm.

XW = 0.35MAC + XW−R | (11.1)

XW = (0.35 × 16.4) + 30.045 = 35.785cm

Wing airfoil maximum thickness is 11.71% of MAC, fuselage height, Hfus is 12cm and landing gear height is 22cm. Therefore, the y-axis coordinate for the wing CG is calculated as:

ZW = (0.5 × (
t
C

⁄ )
max
- MAC) + Hfus + HLG | (11.2)

ZW = (0.5 × 0.1171 × 16.4) + 12 + 22 = 34.96

STEP 5: Fuselage CG Location

The fuselage CG location was calculated to be at 34cm from the nose tip and 6cm. Therefore, Xfus is 38cm from the x-reference line and Zfus is 28cm from z--reference line.

STEP 6: Horizontal Tail CG

Horizontal tail CG is assumed to be at 30% of its MAC. From horizontal tail design, the following results were obtained:

1. Horizontal tail root chord, Chr = 8.44cm
2. Horizontal tail MAC, MACh = 7.24cm
3. Distance from tail root leading edge to wing root leading edge, XHTLE-WLE = 38.82cm
XHT = 0.3MACℎ + (Cℎr − MACℎ) + XHTLE−WLE + XWLE−R | (11.3)

XHT = (0.3 × 7.24) + (8.44 − 7.24) + 38.82 + 30.045 = 72.24cm

The chord line of the horizontal tail coincides with the fuselage center line. Therefore, ZHT is 28cm.

STEP 7: Vertical Tail CG

Vertical tail CG is assumed to be at 30% of its MAC. From vertical tail design, the following results were obtained:

1. Vertical tail root chord, Cvr = 13.1cm
2. Vertical tail MAC, MACv = 11.5cm
3. Distance from tail root leading edge to wing root leading edge, XHTLE-WLE = 37.355cm
XVT = 0.3MACv + (Cvr − MACv) + XVTLE−WLE + XWLE−R | (11.4)

XVT = (0.3 × 11.5) + (13.1 − 11.5) + 37.355 + 30.045 = 72.45cm

Using similar approach as for the wing, ZVT is calculated to be 38.654cm

STEP 8: Main Gear CG Location

The main gear x-CG location coincides with its point of attachment. The aircraft CG was assumed to be at 3.28cm from wing leading edge during landing gear design and main gear was designed to be at 6.5cm from that CG position. Therefore;

XMG = xmg + 3.28 + XWLE−R | (11.4)

XMG = 6.5 + 3.28 + 30.045 = 39.825cm

ZMG is assumed to be 10cm.

STEP 9: Nose Gear CG Location

The wheel base is 32.5cm. Therefore;

XNG = XMG − Br | (11.5)

XNG = 39.825 − 32.5 = 7.325cm

ZNG is assumed to be 8cm.

STEP 10: Engine CG Location

The whole propulsion system CG is at approximately 5.5cm from the x-reference line (i.e. XPS = 5.5cm) and coincides with the fuselage center line (i.e. ZPS = 28cm).

STEP 11: Store CG Location

The store CG is expected to be at the assumed CG location.

XS = 3.28 + XNG | (11.6)

XS = 3.28 + 30.045 = 33.325cm

ZS is 1cm above the fuselage base. Therefore, ZS is 23cm.

STEP 12: Battery CG Location

XBAT is selected to be 16cm and ZBAT is calculated to be 26cm

STEP 13: Other Components CG Location

The location for this is assumed to be at the assumed CG location and 5cm from fuselage base. Therefore, XO is 33.325 and ZO is 26.5cm

STEP 14: Calculation OF CG Location

The masses and CG distances are summarized in the table below

S/N | Component | Mass (g) | XCG (cm) | ZCG (cm)
1 | Fuselage | 211.65 | 38 | 28
2 | Wing | 209.8 | 35.785 | 34.96
3 | Vertical Tail | 30.2 | 72.45 | 378.654
4 | Horizontal Tail | 46.482 | 72.24 | 28
5 | Main Gear | 165.5 | 39.826 | 10
6 | Nose Gear | 120.7 | 7.325 | 8
7 | Propulsion System | 74.5 | 5.5 | 28

8 | Store | 38 | 33.325 | 23
9 | Battery | 240 | 16 | 26
10 | Others | 101 | 33.325 | 27

XCG =

∑ miXCGi

n
i=1
∑ mi

n
i=1

(11.7)

XCG =

mfusXfus + mwingXW + mVTXVT + mHTXHT + mMGXMG + mNGXNG + mPSXPS + mSXS

+mBATXBAT + mOXO

mfus + mwing + mVT + mHT + mMG + mNG + mPS + mS + mBAT + mO

(11.8)

XCG

=

(211.65 × 38) + (209.8 × 35.785) + (30.2 × 72.45) + (46.482 × 72.24) + (165.5 × 39.826) +(120.7 × 7.325) + (74.5 × 5.5) + (38 × 33.325) + (240 × 16) + (101 × 33.325) 211.65 + 209.8 + 30.2 + 46.482 + 165.5 + 120.7 + 74.5 + 38 + 240 + 101

XCG =

37453
1237.8

= 30.257cm

Similarly,

ZCG =

∑ miZCGi

n
i=1
∑ mi

n
i=1

(11.9)

ZCG =

mfusZfus + mwingZW + mVTZVT + mHTZHT + mMGZMG + mNGZNG + mPSZPS + mSZS

+mBATZBAT + mOZO

mfus + mwing + mVT + mHT + mMG + mNG + mPS + mS + mBAT + mO

(11.10)

ZCG =

(211.65 × 28) + (209.8 × 34.96) + (30.2 × 38.654) + (46.482 × 28) + (165.5 × 10) +(120.7 × 8) + (74.5 × 28) + (38 × 23) + (240 × 26) + (101 × 26.5) 211.65 + 209.8 + 30.2 + 46.482 + 165.5 + 120.7 + 74.5 + 38 + 240 + 101

ZCG =

30227
1237.8

= 24.42cm

STEP 15: CG Location on Wing MAC

The CG location on wing MAC is calculated as:

xcg =

XCG−XWLE−R
MAC

(11.11)

Table 11.1: Components masses and CG locations

xcg =

30.257 − 30.045
16.4

= 0.013

This implies that the aircraft CG is at 1.3% of wing MAC

STEP 16: Weight Distribution to Reposition CG Location

In other to reposition the aircraft CG location, some weights have to be repositioned. To keep this simple and easier, battery was repositioned. Via trial and error, when the battery was repositioned to 31.8cm from the reference line, the value of XCG is 33.3216.

xcg =

33.3216 − 30.045
16.4

= 0.1998 ≅ 0.2

Therefore, the aircraft CG, when XBAT is 31.8cm, is located at 20% of wing MAC.

The CG coordinates (x, y, z) using body axis system is (33.32, 0, 24.42) in centimeters from their reference axes.

STEP 17: Stability and Control Check

The lateral, longitudinal and directional stability and control was considered during wing and tail design. The result will remain as considered earlier, since the CG location remains the same.

STEP 18: Aircraft Moment of Inertia Check

The aircraft longitudinal, lateral and directional mass moments of inertia about the x, y and z axis are calculated to be:

Ixxcg = 0.03517Kgm²

, Iyycg = 0.042Kgm² and Izzcg = 0.058Kgm²

STEP 19: Aircraft Components Redesign

The aircraft parameters that changed are the CG coordinates and moments of inertial which were used during landing gear design. The calculated change in the aircraft mass is 37g which might cause some changes in the aircraft performance but its value will be worked with.

With a CG height of 2.42cm from fuselage base and lateral mass moment of inertia about the aircraft cg (Iyycg) of 0.042Kgm²
, the landing gear was redesigned and the following are the new parameters.

LANDING GEAR REVIEWED DESIGN RESULTS

1. Landing gear configuration – Tricycle
2. Landing gear type – Fixed
3. Aircraft CG location – 3.28cm from wing LE
4. CG height from ground – 24.12cm
5. Landing gear height from ground – 21.7cm
6. Mass moment of inertial about main gear, Iyymg = 0.11140Kgm²
7. Main gear distance from CG – 5.06cm
8. Tipback angle – 11.87ᵒ
9. Main gear distance from wing leading edge, XMG-LE – 8.34cm
10. Takeoff rotation clearance – 49.4ᵒ
11. Wheel base – 25.32cm
12. Minimum wheel track – 27.85cm
13. Wheel track based on ground controllability > 25.29cm
14. Overturn angle – 27.67ᵒ
15. Wheel track based on ground stability > 32.85cm
16. Landing gear attachment – under fuselage
17. Nose gear load – 2.93N
18. Main gear load – 10N

# CHAPTER 12

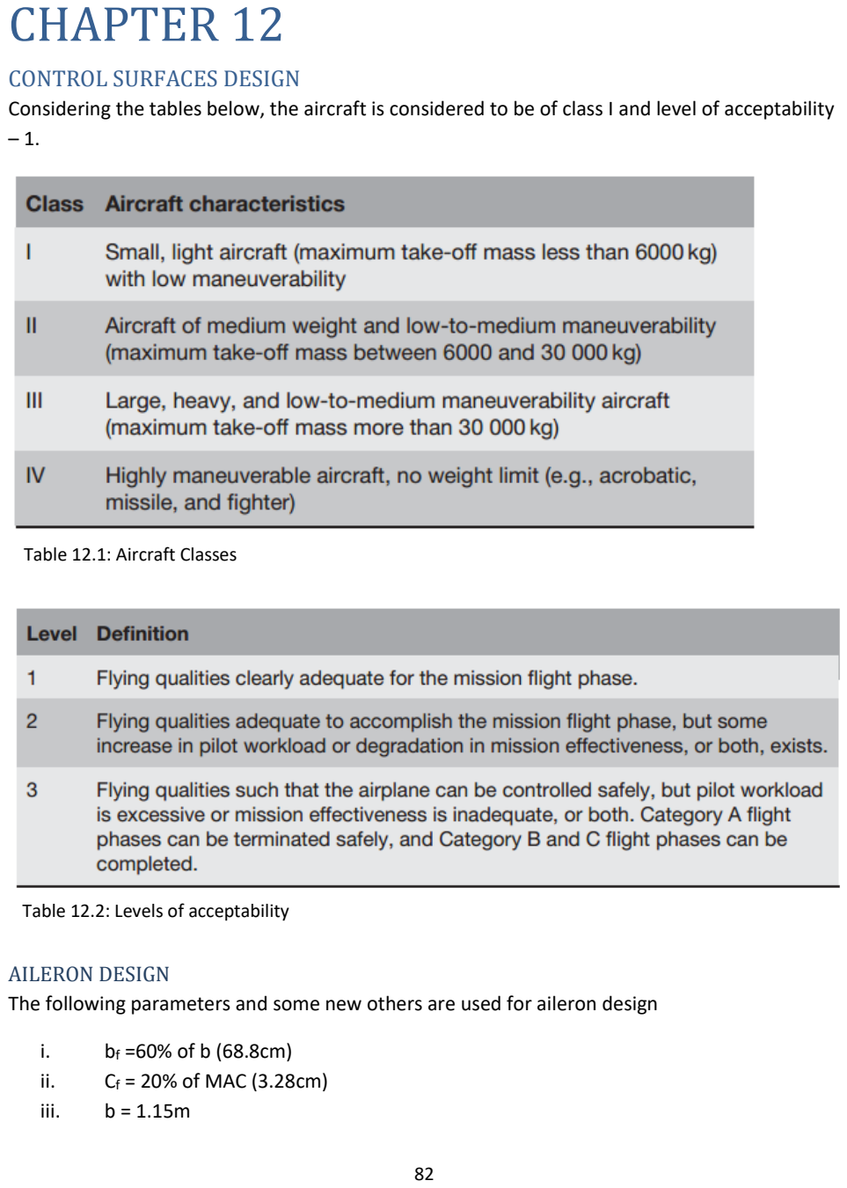
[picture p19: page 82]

CONTROL SURFACES DESIGN
Considering the tables below, the aircraft is considered to be of class I and level of acceptability – 1.

AILERON DESIGN
The following parameters and some new others are used for aileron design
i. bf =60% of b (68.8cm)
ii. | Cf = 20% of MAC (3.28cm)
iii. | b = 1.15m

Table 12.1: Aircraft Classes

Table 12.2: Levels of acceptability iv. C or MAC =Cr = Ct = 16.4cm
v. CLαW = 4.8276rad⁻¹
vi. | S = SW = 0.1878m²
vii. | Sh = 0.0245m²
viii. | SVt = 0.02m²
ix. | λ = 1
x. Vapp or Vland = 10.4m/s
STEP 1: Design Requirement

The following are the requirements the roll control surface should satisfy

i. Maneuverability
ii. | Roll controllability
iii. | Ease of manufacturing
iv. | Low cost
STEP 2: Roll Control Surface Configuration

Due to design simplicity, low cost and ease of manufacturing, Aileron is selected

STEP 3: Maneuverability and Roll Control Requirement

The table below was considered for the requirement which specifies the time to achieve a specific bank angle.

STEP 4: Aircraft Class and Critical Flight Phase for Roll Control

Aircraft class is class I and the critical flight phase for roll control is at the lowest speed (towards landing/approach). From the table below, Landing/approach falls under phase C

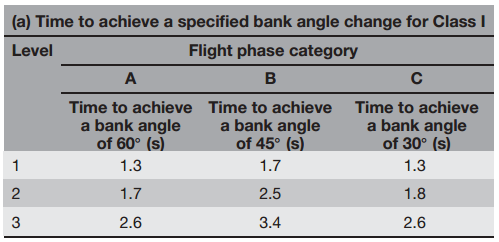
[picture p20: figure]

Table 12.3: Roll control requirement

STEP 5: Handling Quality Design Requirements

The roll control handling qualities design requirement is identified from Table 3, which states that the aircraft in Class I, flight phase C, for a level of acceptability of 1, is required to be able to achieve a bank angle of 30◦ in 1.3 seconds.

STEP 6: Aileron Inboard and Outboard Positions

Considering the flap location, the inboard and outboard aileron locations are tentatively selected to be 70% and 95% of the wing span respectively (i.e. bai/b = 0.7 and bao/b = 0.95)

STEP 7: Aileron Chord to Wing Chord Ratio

Aileron to wing chord ratio, Ca/C is tentatively selected to be 20%.

STEP 8: Aileron Effectiveness Parameter

Table12. 4: Flight phase categories

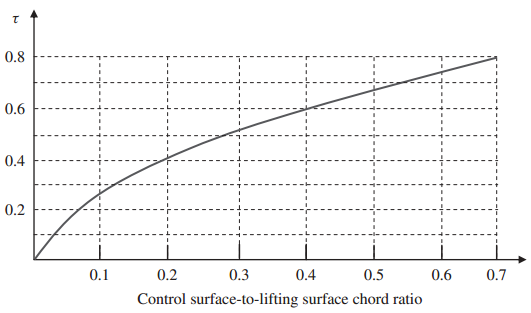
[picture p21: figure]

Figure 12.1: Control surface angle of attack effectiveness parameter

Knowing the aileron chord to wing chord ratio to be 0.2, the aileron effectiveness parameter, τa, was selected to be 0.41 using the table above.

STEP 9: Aileron Rolling Moment Coefficient Derivative

To calculate the aileron rolling moment coefficient derivative, ClδA, the following equation was used.

ClδA

=

2CLαW

τCr
Sb [

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
(12.1)

ClδA

=

2CLαW

τCr
Sb [(

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
) yo
3

) − (

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
) yi
3
)] | (12.2)

Where, CLαW is the wing lift curve slope, τ is the effectiveness parameter, Cr is the wing root chord, S is the wing area, b is the wing span, λ is the wing taper ratio, yo and yi are the inboard and outboard aileron positions respectively, relative to the fuselage centerline.

yo = 0.95 ×

b
2

= 0.95 ×

1.15
2
= 0.5463m | (12.3)

yi = 0.7 ×

b
2

= 0.7 ×

1.15
2
= 0.4025m | (12.4)

ClδA

=

2 × 4.8276 × 0.41 × 0.164

0.1878 × 1.15 [(

0.5463²
2

+

2
3

(

1 − 1

1.15 ) 0.5463³)

− (

0.4025²
2

+

2
3

(

| 1 − 1 1.15 ) 0.4025³)] = 0.2050rad⁻¹
STEP 10: Maximum Aileron Deflection

The maximum aileron deflection, δmax is selected to be ±25ᵒ.

STEP 11: Aircraft Rolling Moment Coefficient

The aircraft rolling moment coefficient, Cl was calculated using the following equation:

Cl = ClδA

- δA | (12.5)

The parameter ClδA is referred to as the aircraft rolling moment coefficient due to aileron deflection derivative and is also called the aileron roll control power and δA is the aileron deflection which is selected to be the maximum deflection in this calculation.

Cl = 0.2050 ×

25
57.3

= 0.0894rad⁻¹

STEP 12: Aircraft Rolling Moment

The aerodynamic rolling moment is generally modeled as a function of the wing area (S), wing span (b), and dynamic pressure (q) as:

LA = qSClb | (12.6)

q =

1
2

ρVT

2 | (12.7)

The critical flight phase is towards landing. Therefore, VT was set to be the equal to Vland (10.4m/s).

q =

1
2
- 1.225 × 10.4

2 = 66.248N/m²

LA = 66.248 × 0.1878 × 0.0894 × 1.15 = 1.2796Nm

STEP 13: Steady-State Roll Rate

The steady state roll rate, PSS was calculated using the following equation:

PSS = √
2∙LA
ρ(SW+Sℎ+SVt)CDR
∙yD

3

| (12.8)

Where SW, Sh and SVt are the wing, horizontal tail and vertical areas, yD is the rolling drag center along the y-axis and the center of gravity and CDR is the aircraft drag coefficient in rolling motion. This coefficient is about 0.7-1.2, which includes the drag contribution of the fuselage.

The areas have been specified earlier, parameter yD is assumed to be 40% of the wing span and CDR is selected to be 0.95.

PSS = √
2 ∙ 1.2796

1.225 ∙ (0.1878 + 0.0245 + 0.02) × 0.95 ∙ (0.4

1.15
2

)

3 = 27.9rad/s

STEP 14: Bank Angle for Steady State Roll Rate

φ =

Ixx
ρ(SW+Sℎ+SVt)CDR
∙yD

3

ln(PSS

2
) | (12.9)

φ1 =

0.03517

1.225 ∙ (0.1878 + 0.0245 + 0.02) × 0.95 ∙ (0.4

1.15
2

)

3

ln(27.9

2
) = 71.18rad (4078.31°)

STEP 15: Aircraft Roll Rate Produced by Aileron Rolling Moment Until Aircraft Reaches Steady State Roll Rate

This parameter is expressed as:

P =

PSS

2
2φ1

(12.10)

P =

27.9

2
2 × 71.8

= 5.47rad/s

2

STEP 16: Time to Reach Desired Bank Angle

The bank angle, φ1 (4078.31ᵒ) is greater than the required bank angle, φreq (30ᵒ) in step 5.

Time to reach the desired bank angle is expressed as:

t2 = √
2φdes
P

(12.11)

t2 = √
2 × 30
5.47 × 57.3

= 0.44s

STEP 17: Roll Time Comparison

The required roll time specified to reach a bank angle of 30ᵒ (in step 5) is 1.3s and the time to achieve this bank angle (as calculated in step 16) is 0.44s. Since the calculated roll time (0.44s) is less than the required roll time (1.3s), the aileron design satisfies the requirement.

STEP 18: Aileron Stall

With the use of a software, XFOIL, the aileron (with a Ca/C = 0.2) at a deflection, δ of 25ᵒ stalls at 8ᵒ angle of attack as shown in the figure below.

STEP 19: Adverse Yaw

Adverse yaw occurs as a result of the difference in the local lift and thus, induced drag on each sides of the wing. This difference in the induced drag gives rise to a corresponding opposite yawing moment which makes the bank/turn not coordinated. To avoid such undesirable yawing motion, the solution selected is to employ a simultaneous aileron/rudder deflection so as to eliminate the adverse yaw which requires an interconnection between the aileron and the rudder.

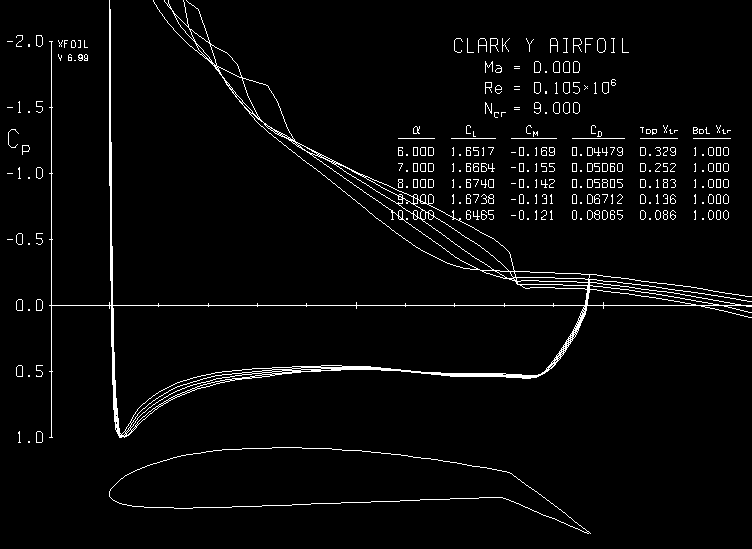
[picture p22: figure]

STEP 20: Aileron Reversal

This is a phenomenon where the wing losses its lift at high speed due to aeroelastic twists and the deflected aileron produces a rolling moment in a reversed direction. The solution selected to avoid this is to make the wing stiffer and to limit aileron deflection to about 17ᵒ at high speed.

STEP 21: Aerodynamic Balance/Mass Balance

The type of aerodynamic balance selected is the overhanging balance – where the hinge line is moved aft (a bit) towards the aileron center of pressure. The leading edge of the control surface will be elliptical. To insure mass balance and avoid flutter, the control surface center of gravity will be moved towards or in front of the hinge line.

STEP 22: Aileron Span, Chord and Area

Aileron span, ba, chord, Ca and area, Aa are calculated as follows:

Figure 12.2: Aileron stall using XFOIL

ba = yo − yi
(12.12)

ba = 0.5463 − 0.4025 = 0.1438m

Ca = 0.2C | (12.13)

Ca = 0.2 × 0.164 = 0.0328m

Sa = 2 × ba × Ca | (12.14)

Sa = 2 × 0.1438 × 0.0328 = 0.0094m²

AILERON DESIGN RESULT

1. yo =54.63cm
2. yi = 40.25cm
3. δmax = 25ᵒ
4. φdes = 30ᵒ
5. t2 = 0.44s
6. adverse yaw solution – simultaneous aileron/rudder deflection
7. aileron reversal – stiffer wing and δmax = 17ᵒ at high speed
8. Aerodynamic balance – overhanging balance with elliptical aileron leading edge.
9. Mass balance – aileron CG movement towards or in front of hinge line.
10. ba = 14.38cm
11. Ca = 3.28cm
12. Sa (both sides) = 0.0094m²

ELEVATOR DESIGN
The following parameters and some new others are used for elevator design:
i. tï =12deg/s²
ii. | Lwf = 10.327N
iii. | D = 1.046N
iv. | T = 1.7045N
v. Mac_wf = – 0.1125Nm
vi. | a = 0.486m/s²
vii. | m =1.2Kg
viii. | xmg-cg = 5.06cm
ix. | xmg – xac_wf = 4.24cm
x. xach – xmg = 32.29cm
xi. | ZD – Zmg = 27.7cm
xii. | ZT – Zmg = 27.7cm

xiii. | Zcg – Zmg = 24.42cm
xiv. | Iyymg = 0.1114Kgm²
xv. | VR = 8.8m/s
xvi. | Sh = 0.0245m²
xvii. | S = 0.1878m²
xviii. MAC = 16.4cm
xix. | αh = -5.12ᵒ
xx. | CLαh = 4.3118rad⁻¹
xxi. | ηh = 0.9
xxii. | VH = 0.3
xxiii. TC = 1.7435N
xxiv. | VC = 14.6154m/s
xxv. | Cmα = -0.83377rad⁻¹
xxvi. | CLα = 4.828rad⁻¹
xxvii. CLC = 0.4798
STEP 1: Elevator Design Requirements
a. Takeoff rotation
b. Longitudinal trim requirement
c. Low cost
d. Manufacturability
STEP 2: Takeoff Rotation Acceleration Requirement – 12deg/s²
STEP 3: Elevator Span

Using the table below as guideline, the elevator span to tail span ratio (bE/bh) is 0.8.

STEP 4: Maximum Elevator Deflection (δE)

From the table above, maximum up deflection (negative) is selected to be -25deg and maximum down deflection (positive) is +20deg.

STEP 5: Wing/Fuselage Lift (Lwf), Aircraft Takeoff Rotation Drag (D) and Wing/Fuselage Pitching Moment (Mac_wf)
i. Lwf =10.327N
ii. | D = 1.046N
iii. | Mac_wf = – 0.1125Nm

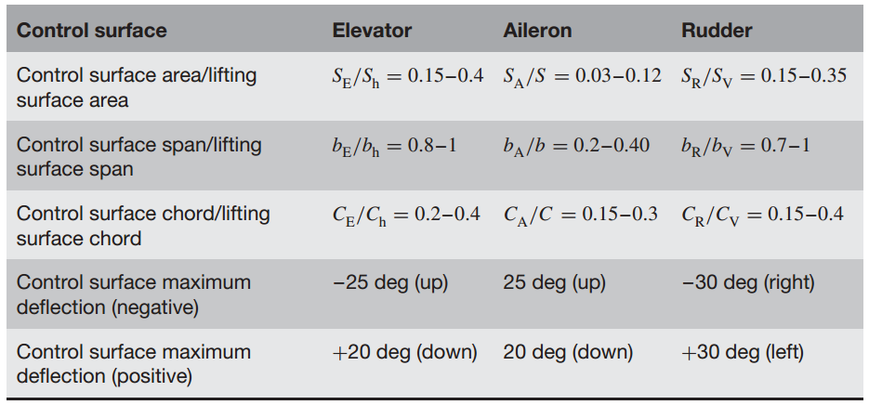
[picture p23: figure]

STEP 6: Aircraft Linear Acceleration during Takeoff – a = 0.486m/s²
STEP 7: Contributing Pitching Moments during Takeoff Rotation

The contributing pitching moments during takeoff rotation are: aircraft weight moment, MW, aircraft drag moment, MD, engine thrust moment, MT, Wing/fuselage lift moment, MLwf, wing/fuselage aerodynamic pitching moment, Mac_wf, and linear acceleration moment, Ma. Since these parameters are considered for takeoff rotation, the moments are about the main gear contact with the ground.

For these calculations, the most forward CG position is to be considered (but the CG position for this design is constant). These moments are calculated as follows.

Mw = W(xmg − xcg) | (12.15)

Mw = 1.2 × 9.81 × 0.0506 = 0.5957Nm

MD = D(ZD − Zmg) | (12.16)

MD = 1.046 × 0.277 = 0.2897Nm

MT = T(ZT − Zmg) | (12.17)

MT = 1.7045 × 0.277 = 0.4721Nm

MLwf = Lwf (xmg − xacwf) | (12.18)

Table 12.5: Typical values for geometry of control surfaces

MLwf = 10.327 × 0.0424 = 0.4379Nm

Ma = m ∙ a(Zcg − Zmg) | (12.19)

Ma = 1.2 × 0.486 × 0.2442 = 0.1424Nm

STEP 8: Desired Horizontal Tail Lift during Takeoff Rotation

The desired horizontal tail lift is expressed as:

Lℎ =

[

Lwf (xmg − xacwf) + Macwf + m ∙ a(Zcg − Zmg) − W(xmg − xcg) + D(ZD − Zmg)

−T(ZT − Zmg) − Iyymg

θ̈

]

xacℎ − xmg

(12.20)

This can be simplified as:

Lℎ =

MLwf+Macwf+Ma−Mw+MD−MT−Iyymgθ̈

xacℎ

−xmg

(12.21)

Since all the parameters of this equation have been gotten already, they were plugged into the equation.

Lℎ =

0.4379 + (−0.1125) + 0.1424 − 0.5957 + 0.2897 − 0.4721 − (0.1114 ×

12
57.3

)

32.29
= −1.0332N
STEP 9: Desired Horizontal Tail Lift Coefficient

CLℎ =

2Lℎ
ρVR

2Sℎ

(12.22)

CLℎ =

2 × (−1.0332)
1.225 × 8.8

2 × 0.0245 = −0.889

STEP 10: Elevator Angle of Attack Effectiveness

The elevator angle of attack effectiveness, τe was obtained from an equation used to model the horizontal tail lift coefficient.

CLℎ = CLαℎ

αℎ + CLαℎ

τeδE | (12.23)

This was rearranged as:

τe =

CLℎ

−CLαℎ

αℎ

CLαℎ

δE

(12.24)

τe =

−0.889 − (4.3118 ×

−5.12
57.3

)

4.3118 ×

−25
57.3

= 0.2678

STEP 11: Elevator-To-Tail Chord Ratio (CE/Ch)

With the value of elevator angle of attack effectiveness obtained above (τe = 0.2678), the elevator chord-to-tail chord ratio is obtained to be 0.096 from the figure below

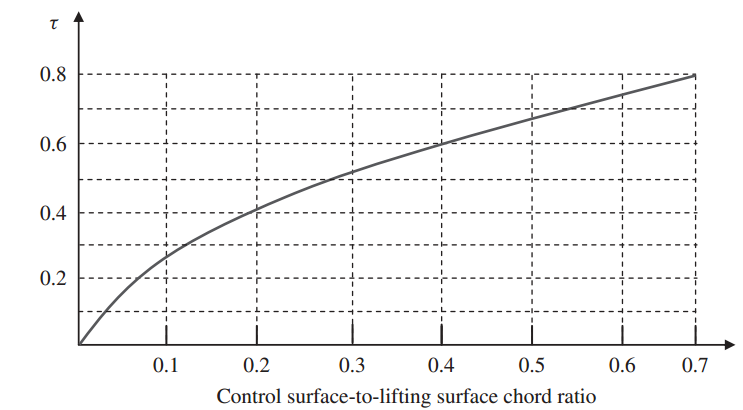
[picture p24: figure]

STEP 12.2: Elevator-To-Tail Chord Ratio (CE/C) Check

Since the value of this ratio (CE/Ch = 0.096) is less than 0.5, an all moving tail won’t be used and the obtained value will be used.
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

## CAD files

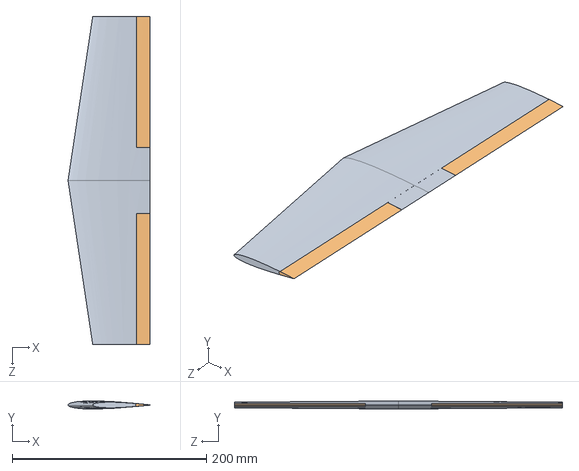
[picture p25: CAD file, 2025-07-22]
solidworks_files/Assembly/Horizontal tail.SLDASM
84.5 x 8.34 x 338.1 mm
Horizontal tail
Elevator

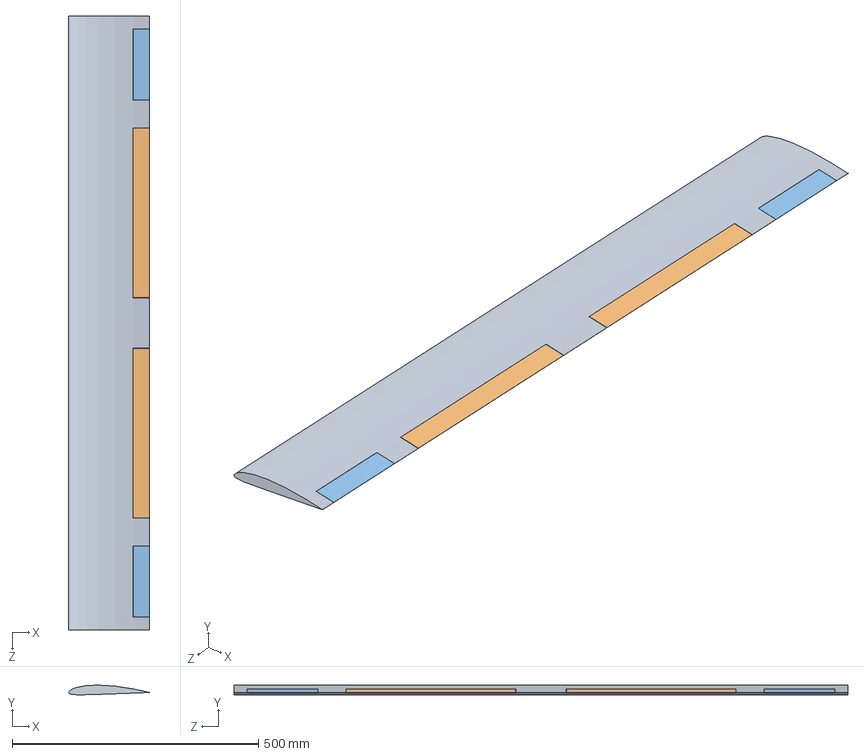
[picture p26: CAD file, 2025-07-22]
solidworks_files/Assembly/Wing.SLDASM
164.1 x 19.9 x 1246.6 mm
Wing_clark y
Flap_clark y x 2
Aileron_clark y x 2

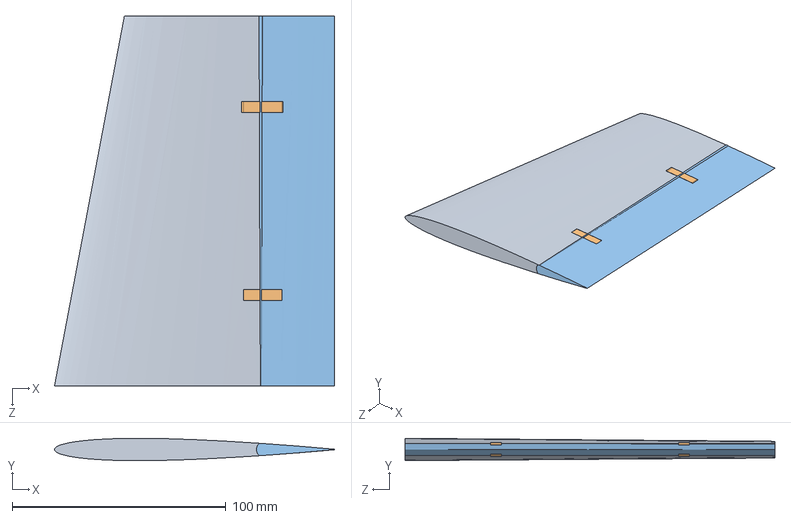
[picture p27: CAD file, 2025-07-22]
solidworks_files/Assembly/Vertical tail.SLDASM
131.1 x 10.5 x 173.0 mm
Vertical tail - rudder cut
Vertical tail - Rudder hinge x 2
Rudder

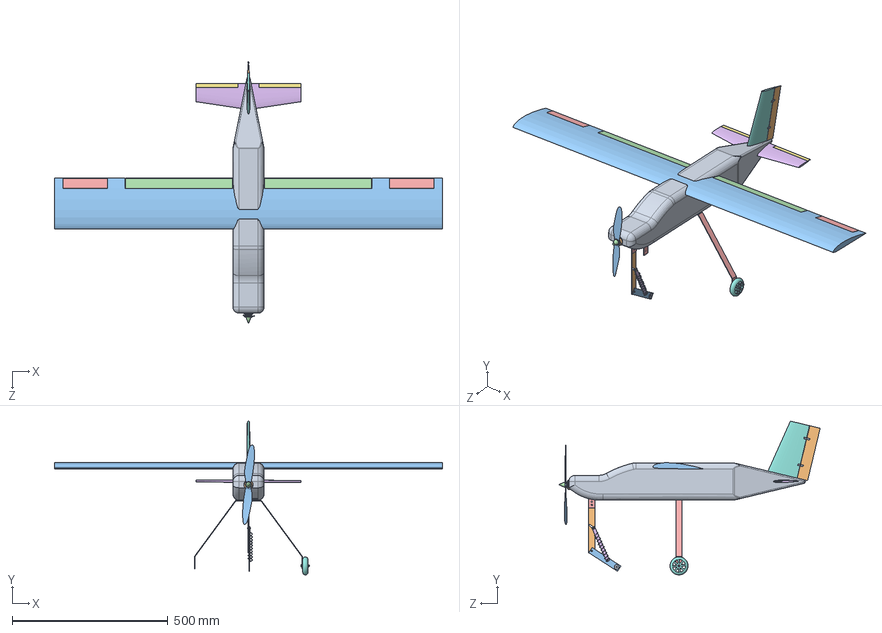
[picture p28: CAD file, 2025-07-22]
solidworks_files/Assembly/UAV.SLDASM
1246.6 x 494.2 x 839.7 mm
Fuselage
Electric motor
Propeller - 30deg twist
Propeller spinner
Wing_clark y
Flap_clark y x 2
Aileron_clark y x 2
Horizontal tail
Elevator
Vertical tail - rudder cut
Vertical tail - Rudder hinge x 2
Rudder

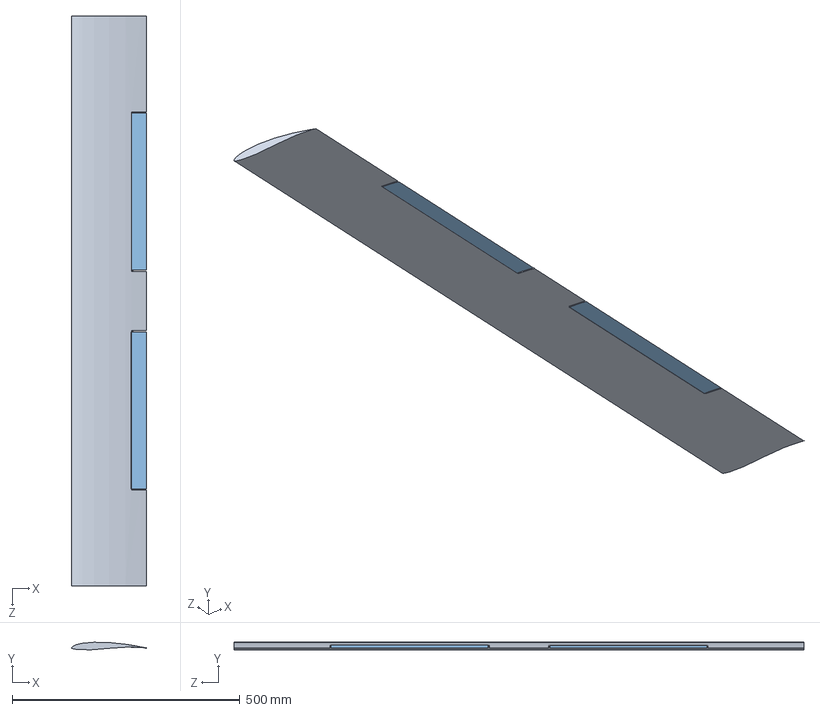
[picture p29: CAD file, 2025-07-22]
solidworks_files/wing assembly.SLDASM
164.0 x 16.6 x 1250.0 mm
Full wing
flap spar x 2
Flap x 2

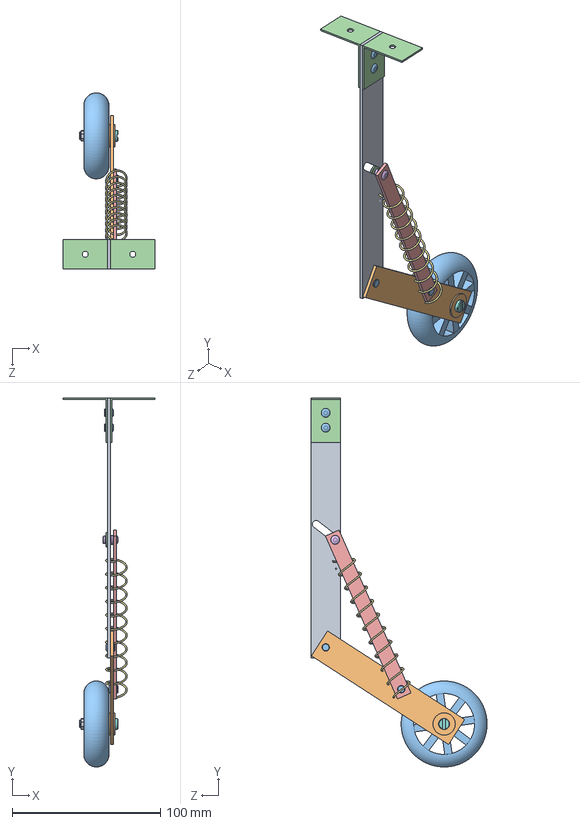
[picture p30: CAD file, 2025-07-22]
solidworks_files/nose_gear/Nose gear.SLDASM
62.0 x 248.6 x 118.7 mm
Vertical component
Slant component
Fuselage attachment x 2
End of travel - EOT rod
Rivet 2
Part8^Nose gear
Bolt
Nut
Tire washer x 2
Tire
E.O.T. washer

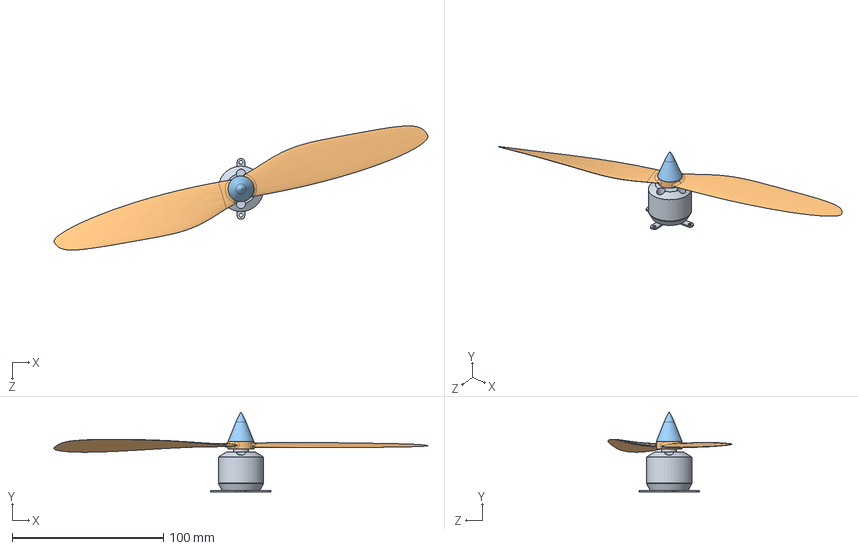
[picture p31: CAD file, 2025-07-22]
solidworks_files/Propulsion system assembly.SLDASM
247.4 x 52.9 x 82.1 mm
Electric motor
Propeller - 30deg twist
Propeller spinner

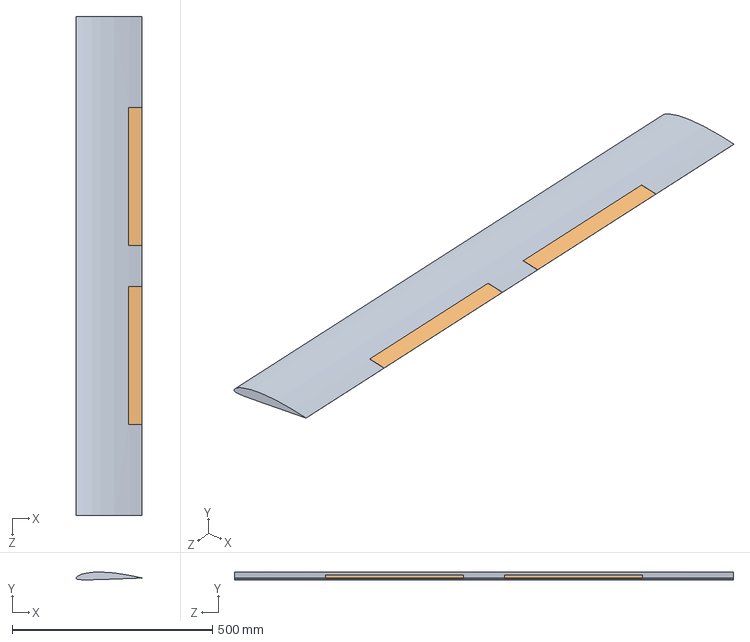
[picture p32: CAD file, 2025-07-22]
solidworks_files/Wing with flap clark y.SLDASM
164.1 x 19.9 x 1246.6 mm
Wing_clark y
Flap_clark y x 2

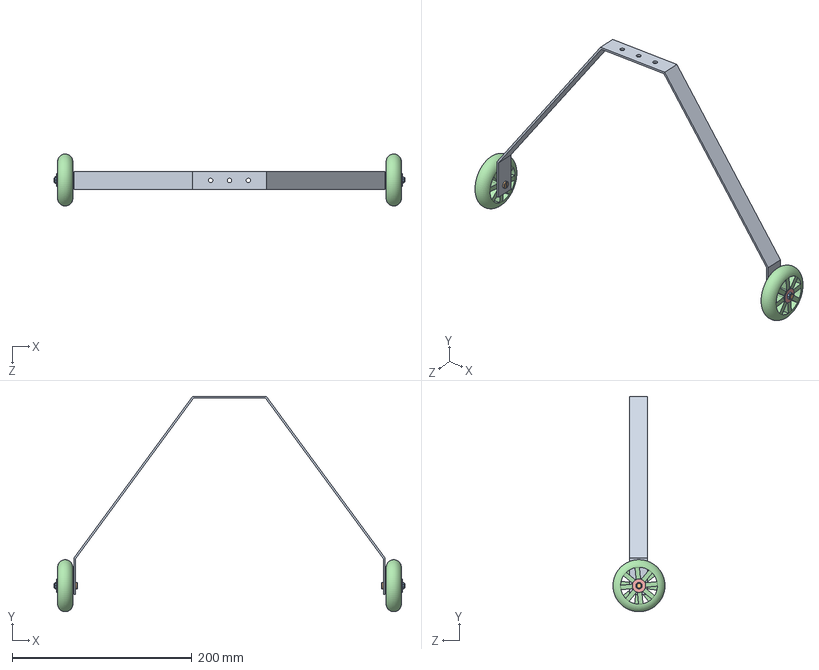
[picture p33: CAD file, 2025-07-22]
solidworks_files/Main gear assembly.SLDASM
390.9 x 239.9 x 57.9 mm
Main Gear
Bolt x 2
Nut x 2
Tire x 2
Washer x 4

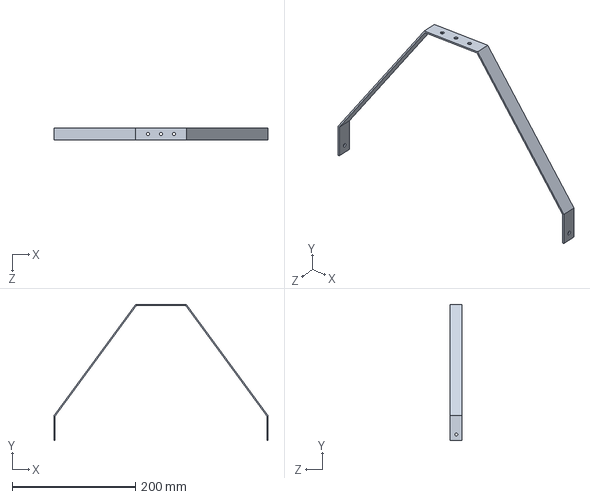
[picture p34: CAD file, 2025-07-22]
solidworks_files/Main Gear.SLDPRT
346.9 x 220.9 x 20.0 mm

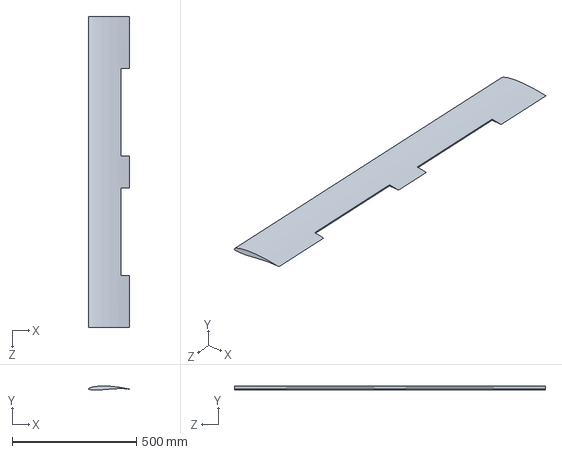
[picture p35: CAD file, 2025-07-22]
solidworks_files/Full wing.SLDPRT
164.0 x 16.6 x 1250.0 mm

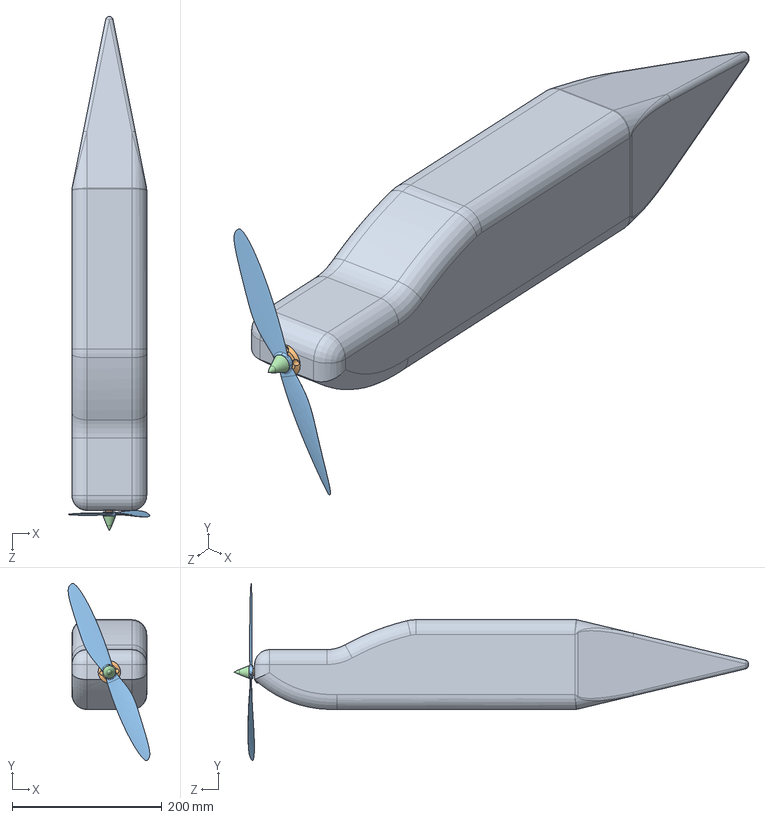
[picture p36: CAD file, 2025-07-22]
solidworks_files/Fuselage - propulsion system assembly.SLDASM
109.2 x 237.0 x 686.8 mm
Fuselage for propulsion system
Electric motor
Propeller - 30deg twist
Propeller spinner

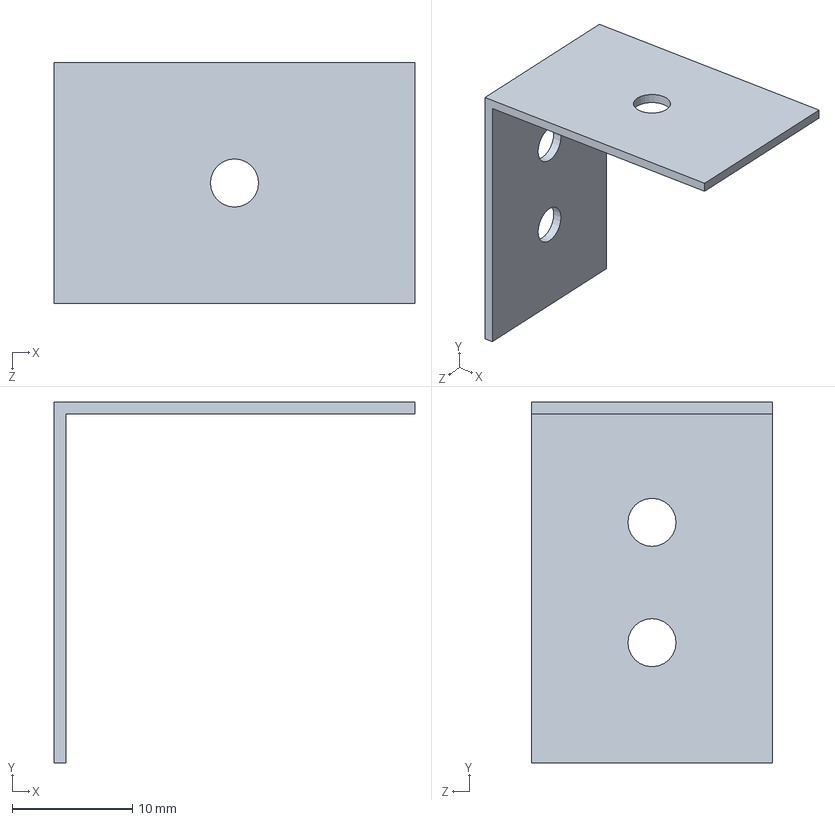
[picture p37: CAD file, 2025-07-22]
solidworks_files/nose_gear/Fuselage attachment.SLDPRT
30.0 x 30.0 x 20.0 mm

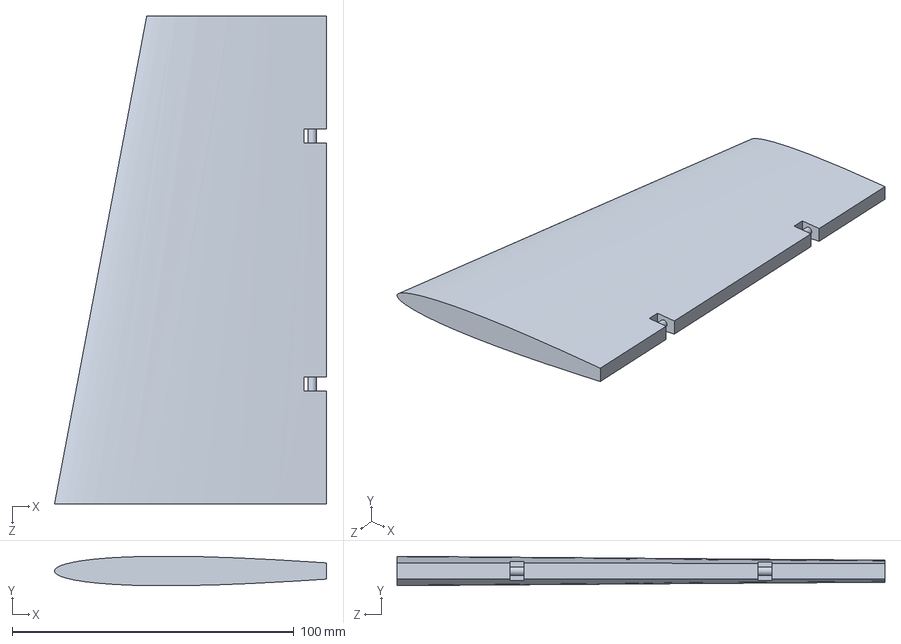
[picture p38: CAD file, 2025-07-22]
solidworks_files/Vertical tail - rudder cut.SLDPRT
96.5 x 10.5 x 173.0 mm

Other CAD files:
solidworks_files/Tire.SLDPRT
solidworks_files/nose_gear/Fillet.SLDPRT
solidworks_files/Propeller - 30deg twist.SLDPRT
solidworks_files/nose_gear/Rivet 2.SLDPRT
solidworks_files/Aileron_clark y.SLDPRT
solidworks_files/Assembly/Horizontal tail.SLDPRT
solidworks_files/Bolt.SLDPRT
solidworks_files/Electric motor.SLDPRT
solidworks_files/Elevator.SLDPRT
solidworks_files/FUSELAGE_NEW.SLDPRT
solidworks_files/FUSELAG_NEW Copy.SLDPRT
solidworks_files/Flap.SLDPRT
solidworks_files/Flap_clark y.SLDPRT
solidworks_files/Fuselage for propulsion system.SLDPRT
solidworks_files/Fuselage.SLDPRT
solidworks_files/HT MAC (7.24cm).SLDPRT
solidworks_files/Horizontal tail NACA 0010.SLDDRW
solidworks_files/Horizontal tail NACA 0010.SLDPRT
solidworks_files/Nut.SLDPRT
solidworks_files/Part2.SLDPRT
solidworks_files/Propeller spinner.SLDPRT
solidworks_files/Propeller.SLDPRT
solidworks_files/Rudder.SLDPRT
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
